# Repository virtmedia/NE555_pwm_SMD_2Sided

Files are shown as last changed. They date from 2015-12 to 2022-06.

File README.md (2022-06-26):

# NE555_pwm_SMD_2Sided
Smallest version of NE555 PWM generator. Designed to make at home.

Here is two-side version of [this](https://github.com/virtmedia/NE555_pwm_SMD) project.

## Description
Simple, small and cheap PWM regulator on NE555.
You can use it to drive 12V motor, LED strip, Peltier module, lightbulb etc.
PCB dimensions: 16.18 x 18.42 mm. 
Pulse width regulated by standard potentiometer.
You can use any Mosfet in DPAK (TO-252) case as You like and follow your requirements. I am using 2SK3918 from old pc motherboard.

If you want to make it, just download the pdf files , print it and make thermotransfer.
All SMD resistors and capacitors (except C2 on power input, with is 1206, so you can use higher capacity) are in 0603 cases.
You have to make connection between two layers of copper where the vias are.

Supply Voltage: 4.5 - 16V
Current consumption: about 20mA with no load
Output current: depending of used mosfet, limited by traces width - you can reinforce it with wire for more current.
PWM frequency: about 1KHz for the parts values as in schematic. You can adjust them, just keep the conciderations in NE555 datasheet.

Note that due to the construction, there is no full 0-100% regulation. The output goes to the almost 100%, but the bottom limit is a little bit above 0%. 

## Status
  Tested & works well :)
  Files are prepared for the production. Gerber files are generated. The order was received from the jlcpcb:
  
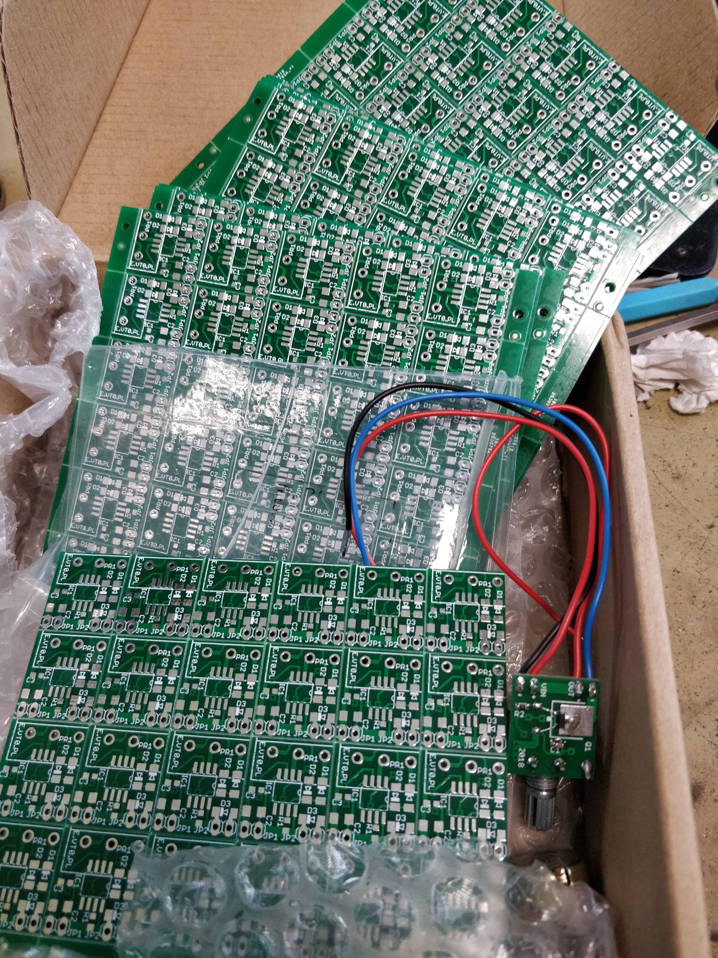
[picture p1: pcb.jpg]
Photo of the PCB
  

## Schematic:

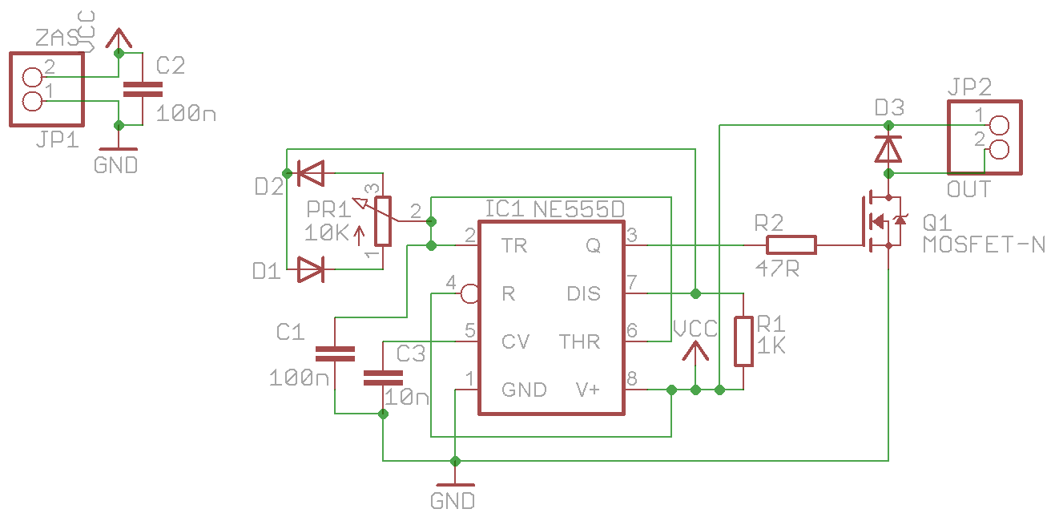
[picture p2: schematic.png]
schematic image
  

## PCB layout:

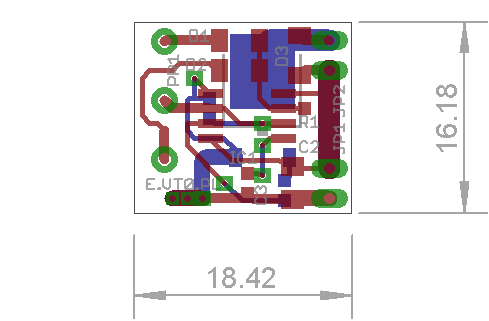
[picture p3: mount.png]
PCB layout image
  
  
## BOM
  
* C1   100n 0603 case
* C2   100n-10u 0805-1206 case
* C3   10n 0603 case 
* D1   LL4148 MINIMELF
* D2   LL4148 MINIMELF                    
* D3   LL4148 MINIMELF              
* IC1  NE555D SO-8
* PR1  10K linear potentiometer
* Q1   Generic MOSFET-N in TO252 (DPAK) case                                 
* R1   1K 0603 case
* R2   47R 0603 case
  
## Future
The project looks finished, i have no plan to change it.

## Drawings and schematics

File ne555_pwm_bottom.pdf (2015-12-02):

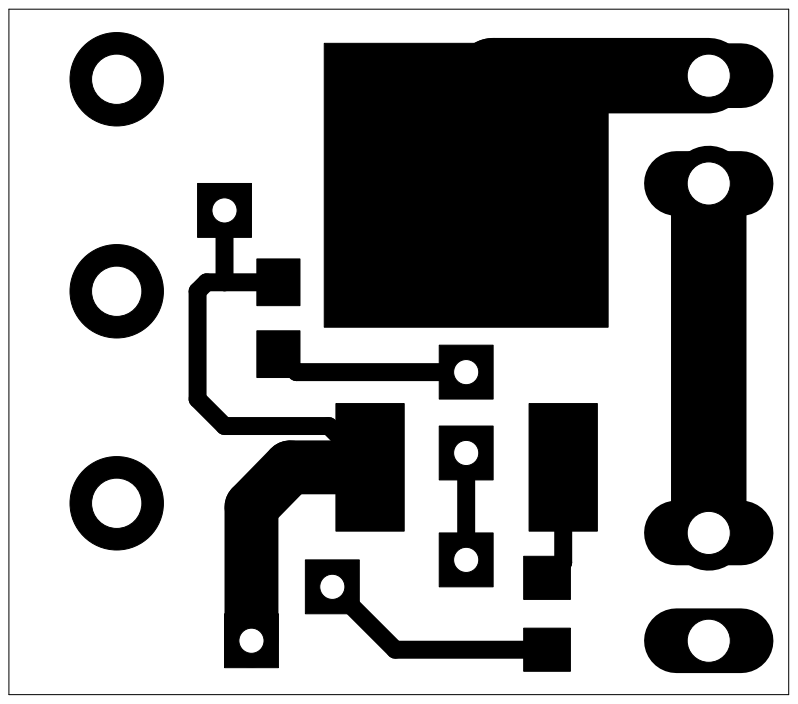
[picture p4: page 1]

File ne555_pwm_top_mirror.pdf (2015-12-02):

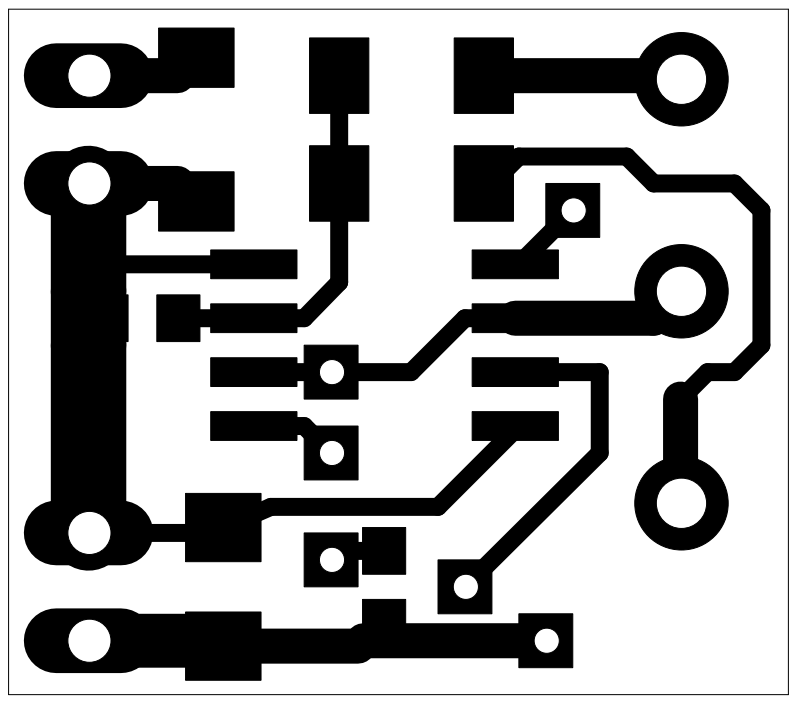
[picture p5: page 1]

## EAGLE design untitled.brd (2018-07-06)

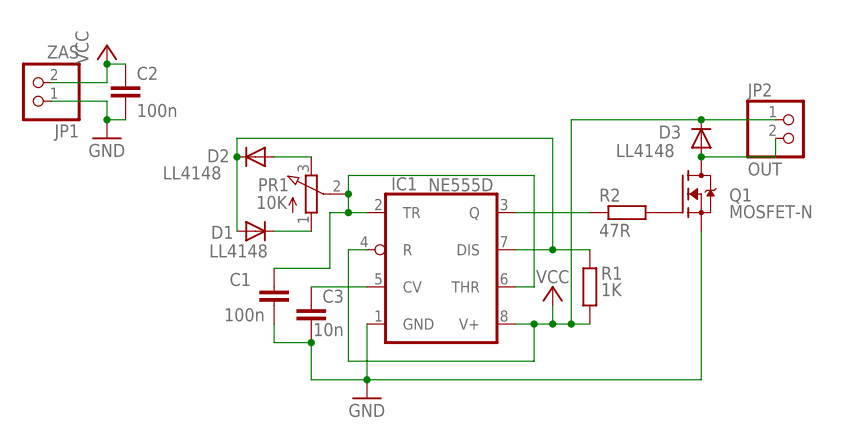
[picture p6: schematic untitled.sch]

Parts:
C1: 100n; C0603
C2: 100n; C1206
C3: 10n; C0603
D1, D2, D3: LL4148; MINIMELF
IC1: NE555D; SO08
JP1: ZAS; 1X02
JP2: OUT; 1X02
PR1: 10K; 3RP/1610N
Q1: MOSFET-N; TO252
R1: 1K; R0603
R2: 47R; R0603

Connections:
GND: C1.2, C2.2, C3.2, IC1.1 (GND), JP1.1, Q1.2 (S)
unnamed: C1.1, IC1.2 (TR), IC1.6 (THR), PR1.2 (S)
unnamed: D1.C, PR1.1 (A)
unnamed: D2.A, PR1.3 (E)
unnamed: D1.A, D2.C, IC1.7 (DIS), R1.2
unnamed: IC1.3 (Q), R2.1
unnamed: Q1.1 (G), R2.2
unnamed: C3.1, IC1.5 (CV)
unnamed: D3.A, JP2.2, Q1.3 (D)
VCC: C2.1, D3.C, IC1.4 (R), IC1.8 (V+), JP1.2, JP2.1, R1.1

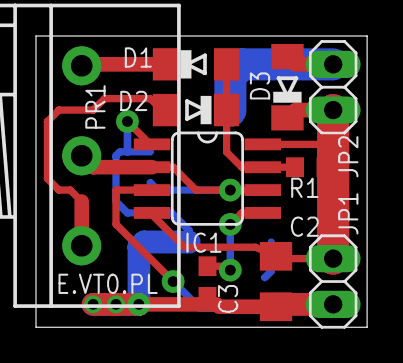
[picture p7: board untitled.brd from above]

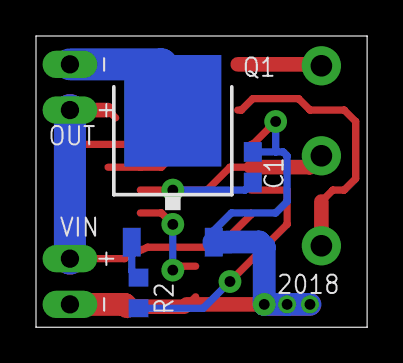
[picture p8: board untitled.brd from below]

Board: 2 copper layers, 18.4 x 16.2 mm, 13 parts (3 on the bottom side), 10 nets.

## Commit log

2015-12-02 added image with mount schematic
    [untitled.brd]
2018-07-06 Prepared for prodution
    [untitled.brd, untitled.sch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]
2018-07-06 Description update
    [untitled.brd, untitled.sch]
